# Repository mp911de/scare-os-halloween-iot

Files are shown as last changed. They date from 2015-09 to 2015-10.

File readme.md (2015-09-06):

ScareOS Halloween Pumpkin thingy
================================

Muhahahaha! Aaaaargh! Trick or Treat. Be so sweet. Give me something good to eat.

I wanted to build something cool and scary for Halloween. Here in Germany Helloween is just about to become a trend. Meet the ScareOS, a thingy to spice up Halloween.

**Features**

* Moving eyes (object tracking perhaps in version 2 - have to figure out how to integrate motion tracking)
* Discovers if someone is around by using a ranging sensor
* Plays Halloween sounds when it's awake
* Sleep state if no one is around for a while
* Whines when someone comes too close

ScareOS is an Arduino-based thingy with eyes, sound and a range sensor. ScareOS tends to be sleepy. It there's no one around, it sleeps and snores. As soon as someone comes into range, it awakens. Then the thingy looks at its visitor, triggers a series of Halloween sounds and, moves its eyes. But beware! It starts to cry like a baby when you approach too close.

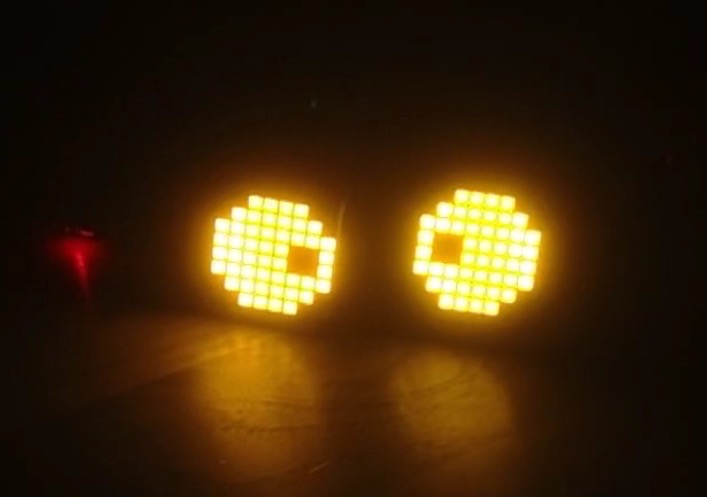
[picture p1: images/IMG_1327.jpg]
Glow in the dark


The components are not yet built into a Pumpkin, but they are ready to go. I'll provide pictures on Oct 31, once I got the pumpkin set up.

**Youtube Videos**

<a href="http://www.youtube.com/watch?feature=player_embedded&v=ZoHyhjCuUWQ
" target="_blank"></a>

<a href="http://www.youtube.com/watch?feature=player_embedded&v=dUIu-4qToRM
" target="_blank"></a>

*Hint: The video interferences are some recording issues.*

Ingredients
-----
You'll need:

* 1x Arduino (I used the [Ardunino Mini Pro](http://www.adafruit.com/products/2378) because of its form factor)
* 1x [Ultrasonic HC-SR04 Ranging Sensor](http://www.amazon.com/SainSmart-HC-SR04-Ranging-Detector-Distance/dp/B004U8TOE6)
* 2x [8X8 LED Matrix with I2C Backpack](http://www.adafruit.com/products/1050)
* 1x [Audio FX Sound Board - WAV/OGG Trigger with 2MB Flash](http://www.adafruit.com/products/2133)
* 1x 470µF Capacitor
* 1x 470Ω - 560Ω Resistor
* 1x 330Ω - 360Ω Resistor
* a [whole bunch](http://www.adafruit.com/products/826) of wire connectors
* 1x [Speaker](http://www.adafruit.com/products/1314)
* 1x [Breadboard](http://www.adafruit.com/products/64) (or a circuit board)

Once you have all parts together, you can start wiring them.

Wiring
------
The common ground and common `VCC` of the breadboard comes handy to provide current for the involved components. The diagram shows you how to connect the particular components.

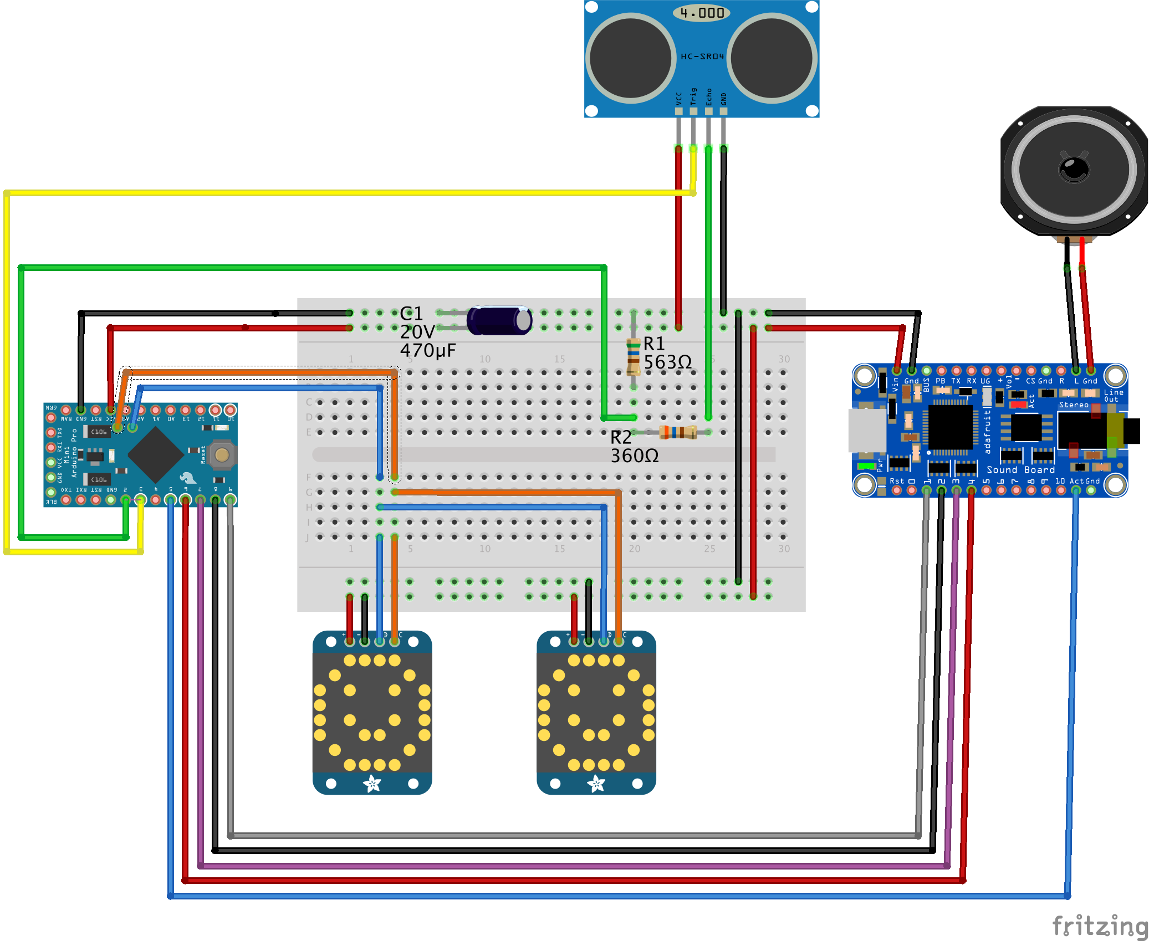
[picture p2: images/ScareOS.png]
Fritzing wiring diagram


The two resistors protect the circuit from a signal that won't come back. I originally built the ranging sensor circuit on RaspberryPi and took kept the design. The Arduino `pulseIn()` function also accepts a timeout so basically the circuit would work without the resistors.

The capacitor stabilizes the circuit. I discovered that the LED matrices cause some interference and instabilities within the `VCC`. The effect: The ranging sensor works only until some 80cm once both LED matrices are turned on. If the matrices are switched off or do not display anything, the ranging sensor works fine. My solution: Connect a capacitor to `GND` and `VCC`.

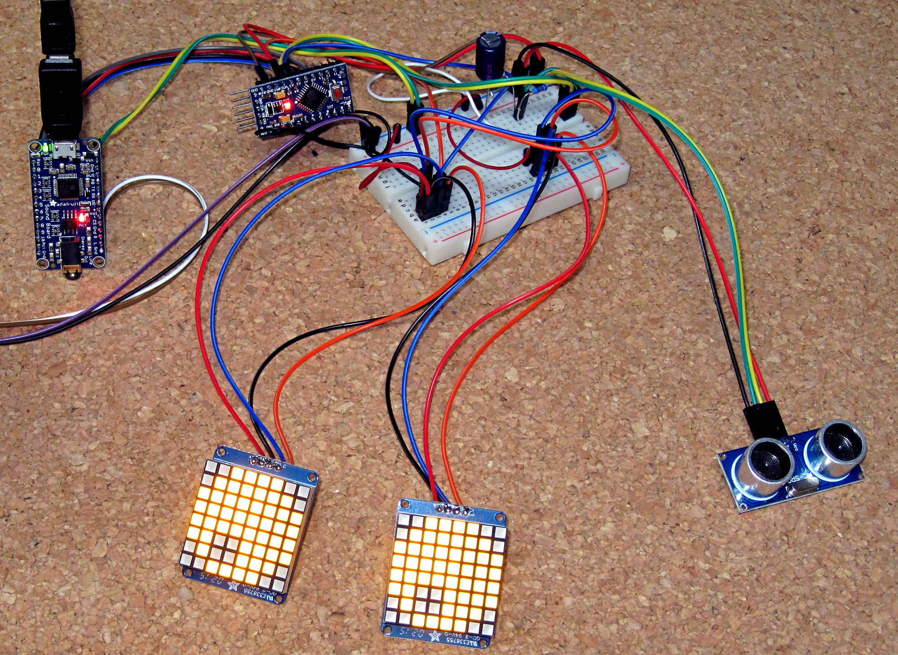
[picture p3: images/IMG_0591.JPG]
Connected components


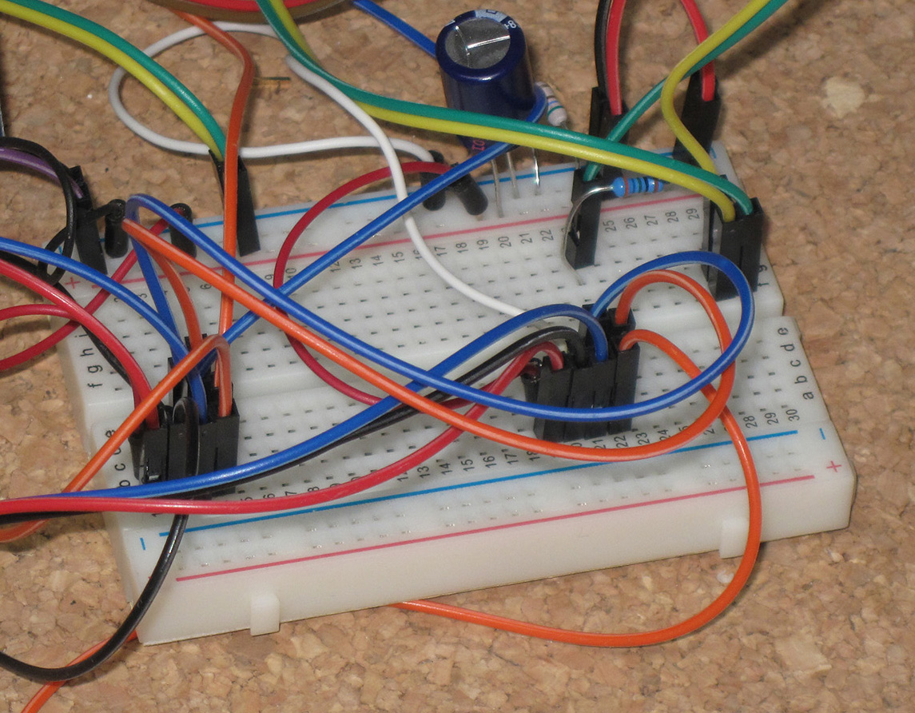
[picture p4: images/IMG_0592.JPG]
Closeup of the breadboard


Sounds
------
Once all parts are connected, upload the sounds from the `sounds` folder to the soundboard. Connect the soundboard to a USB port and copy all files to the flash disk using your favorite file copy tool.

There are four sounds/categories of sounds:

1. T01 Wake-up sound: Played once the ScareOS awakes from the sleep state
2. T02RANDnn sounds: Collection of sounds that are played randomly in the awake state. Therefore, the special suffix `RAND00` to `RAND99`
3. T03 sound: Whining/crying if someone approaches in the near zone of the device
4. T04HOLDL: Snoring sound, plays as long as the trigger is held, therefore, the special suffix `HOLDL`

Arduino Sketch
--------------

You need some code to run ScareOS. The code controls the components and handles wake/sleep, triggering sounds and displaying the eyes on the LED matrix.

The code is located in `scare-os/scare-os.ino`. You need two additional libraries:

* [Adafruit-LED-Backpack-Library](https://github.com/adafruit/Adafruit-LED-Backpack-Library)
* [Adafruit-GFX-Library](https://github.com/adafruit/Adafruit-GFX-Library)

The Adafruit site has a nice tutorial how to [install Arduino libraries](https://learn.adafruit.com/adafruit-all-about-arduino-libraries-install-use/arduino-libraries).

So open the Sketch, compile it and upload it to your Arduino.

You can adopt the code to use different pins or adjust the distance/timing:

```arduino
#define PIN_SONIC_TRIGGER 3
#define PIN_SONIC_ECHO 2

#define PIN_SND_TRIGGER_WAKE 9
#define PIN_SND_TRIGGER_REGULAR 8
#define PIN_SND_TRIGGER_NEAR 7
#define PIN_SND_TRIGGER_SLEEPING 6
#define PIN_SND_ACTIVE  5

// ms
#define SOUND_INTERVAL_MS 20000
#define WAKE_DURATION_MS 180000

#define ACTIVATION_DISTANCE_CM 280
#define NEAR_DISTANCE_CM 100
```

### Threading with Arduino

Arduino code runs only single-threaded, meaning your Arduino can do only one thing at a time. The sound trigger module, for instance, does not occupy the Arduino once a sound plays. So sounds play in the background within this terminology. Why am I telling you that? 

Displaying and animating graphics, like it is done with the matrix eyes, requires the Arduino to execute code, sleep a while, then execute code again and so on. One animation cycle lasts between 0.5sec and 10sec. In this time, the Arduino is occupied with the animation. If someone walks by the range sensor really fast, we would not notice it, because we're occupied with animating and not with measuring distance. 

But that's not fully true. Most of the time, the Arduino "sleeps" which means we could use that time to do different things - things like triggering a sound or measuring distance. The code is written to utilize these delays. You'll find lots of calls to a `bgProcessing()` method. This method is called with a delay parameter. If the delay is long enough to measure the distance (measuring the distance needs time and triggering sound, too), the distance is measured and the sound processing is invoked there. It's not exactly a task scheduler like a Windows or MacOS use to emulate multi-threading on one CPU (core), but it interleaves tasks in a similar way.

### Some words about measuring distance

The ranging sensor uses the physics of [speed of sound](https://en.wikipedia.org/wiki/Speed_of_sound) to determine the distance. An ultrasonic sound is triggered and the microphone records the echo. The speed of sound in dry air is about one kilometer in 2.914 sec. Since the sound needs to hit an object that bounces it back, the way is crossed twice. This means, that the duration to measure the distance is `DISTANCE * Speed of Sound * 2`.

Sometimes, the ranging sensor reports an echo after a shorer or longer time. The result of that are flickering distances of up to 100cm. These are outliers and falsify the result (the assumption of distance). The code, therefore, performs a series of measures, sorts the results and takes some middle result. It works pretty good and the implementation is quite simple (easier than calculating a quantile).

And now, it's time to scare:

<a href="http://www.youtube.com/watch?feature=player_embedded&v=ZoHyhjCuUWQ
" target="_blank"></a>

Attribution
-----------
I used following sound effects that require attribution:

* http://soundbible.com/1363-Angry-Cat.html
* http://soundbible.com/1939-Bats-In-Cave.html
* http://soundbible.com/2038-Demon-Girls-Mockingbird.html
* http://soundbible.com/1627-Female-Scream-Horror.html
* http://soundbible.com/1738-Little-Demon-Girl-Song.html
* http://soundbible.com/1828-Poltergeist.html
* http://soundbible.com/1918-Sick-Villain.html
* http://soundbible.com/766-Slow-Breathing.html
* http://soundbible.com/2016-Thunder-Strike-2.html

License
-----------
<br /><span xmlns:dct="http://purl.org/dc/terms/" property="dct:title">ScareOS</span> by <a xmlns:cc="http://creativecommons.org/ns#" href="https://github.com/mp911de/scare-os-halloween-iot" property="cc:attributionName" rel="cc:attributionURL">https://github.com/mp911de/scare-os-halloween-iot</a> is licensed under a <a rel="license" href="http://creativecommons.org/licenses/by/4.0/">Creative Commons Attribution 4.0 International License</a>.<br />Based on a work at <a xmlns:dct="http://purl.org/dc/terms/" href="https://github.com/mp911de/scare-os-halloween-iot" rel="dct:source">https://github.com/mp911de/scare-os-halloween-iot</a>.

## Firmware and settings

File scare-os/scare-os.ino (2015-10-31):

#include <Wire.h>
#include "Adafruit_LEDBackpack.h"
#include "Adafruit_GFX.h"

#define PIN_SONIC_TRIGGER 3
#define PIN_SONIC_ECHO 2

#define PIN_SND_TRIGGER_WAKE 9
#define PIN_SND_TRIGGER_REGULAR 8
#define PIN_SND_TRIGGER_NEAR 7
#define PIN_SND_TRIGGER_SLEEPING 6
#define PIN_SND_ACTIVE  5

Adafruit_8x8matrix matrix1 = Adafruit_8x8matrix();
Adafruit_8x8matrix matrix2 = Adafruit_8x8matrix();

// define eye ball without pupil
byte eyeBall[8] = {
  B00111100,
  B01111110,
  B11111111,
  B11111111,
  B11111111,
  B11111111,
  B01111110,
  B00111100
};

byte eyePupil = B11100111;

// stores current state of LEDs
byte eyeCurrent[8];
int currentX;
int currentY;


// min and max positions
#define MIN -2
#define MAX  2

// delays
#define DELAY_BLINK 40

// perform an effect every # of loop iterations, 0 to disable
#define EFFECT_ITERATION 4

// ms
#define SOUND_INTERVAL_MS 20000
#define WAKE_DURATION_MS 180000

#define ACTIVATION_DISTANCE_CM 280
#define NEAR_DISTANCE_CM 100

boolean awake = true;
long activatedMillis = 0;
long lastSound = 0;
boolean soundStarted = false;
long currentDistance = 0;

void setup() {
  Serial.begin(9600);
  Serial.println("Time to power up");
  
  
  Serial.println("       __J\"L__");
  Serial.println("   ,-\"`--...--'\"-.");
  Serial.println("  /  /\\       /\\  \\");
  Serial.println(" J  /__\\  _  /__\\  L");
  Serial.println(" |       / \\       |");
  Serial.println(" J    _  \"\"\"  _    F");
  Serial.println("  \\   \\|/\\_/\\|/   /");
  Serial.println("   \"-._\\/\\_/\\/_,-\"happy halloween!");
  

  pinMode(PIN_SONIC_TRIGGER, OUTPUT);
  pinMode(PIN_SONIC_ECHO, INPUT);

  pinMode(PIN_SND_TRIGGER_REGULAR, OUTPUT);
  pinMode(PIN_SND_TRIGGER_WAKE, OUTPUT);
  pinMode(PIN_SND_TRIGGER_NEAR, OUTPUT);
  pinMode(PIN_SND_TRIGGER_SLEEPING, OUTPUT);
  pinMode(PIN_SND_ACTIVE, INPUT);

  digitalWrite(PIN_SND_TRIGGER_REGULAR, HIGH);
  digitalWrite(PIN_SND_TRIGGER_WAKE, HIGH);
  digitalWrite(PIN_SND_TRIGGER_NEAR, HIGH);
  digitalWrite(PIN_SND_TRIGGER_SLEEPING, HIGH);

  matrix1.begin(0x70);  // pass in the address
  matrix2.begin(0x71);  // pass in the address

  // LED test
  // vertical line
  byte b = B10000000;
  for (int c = 0; c <= 7; c++)
  {
    for (int r = 0; r <= 7; r++)
    {
      setRow(0, r, b);
      setRow(1, r, b);
    }
    b = b >> 1;
    writeMatrix();
    delay(20);
  }
  // full module
  b = B11111111;
  for (int r = 0; r <= 7; r++)
  {
    setRow(0, r, b);
    setRow(1, r, b);
  }

  writeMatrix();

  // clear both modules
  matrix1.setBrightness(16);
  matrix1.clear();
  matrix2.setBrightness(16);
  matrix2.clear();
  delay(500);

  // random seed
  randomSeed(analogRead(0));

  // center eyes
  displayEyes(0, 0);
  activatedMillis = 0;
  Serial.println("ScareOS ready.");
}

/*
  Arduino loop
*/
void loop()
{

  long awakeDurationMs = getAwakeDurationMs();

  if (awakeDurationMs > WAKE_DURATION_MS) {
    if (awake) {
      awake = false;
      Serial.println("Going to sleep");
      moveEyes(0, -4, 10);
      reduceBrightness();
    }
  }

  if (!awake) {
    slightGlow();
    bgProcessing(random(5, 7) * 500);
    return;
  }

  matrix1.setBrightness(16);
  matrix2.setBrightness(16);

  // move to random position, wait random time
  moveEyes(random(MIN, MAX + 1), random(MIN, MAX + 1), 50);
  bgProcessing(random(5, 7) * 500);

  // blink time?
  if (random(0, 5) == 0) {
    bgProcessing(500);
    blinkEyes();
    bgProcessing(500);
  }

  int effect = random(0, 10);
  switch (effect) {
    case 0: // cross eyes
      crossEyes();
      break;

    case 1: // round spin
      roundSpin(2);
      break;

    case 2: // crazy spin
      crazySpin(2);
      break;

    case 3: // meth eyes
      methEyes();
      break;

    case 4: // lazy eye
      lazyEye();
      break;

    case 5: // crazy blink
      blinkEyes(true, false);
      blinkEyes(false, true);
      break;

    case 6: // glow
      glowEyes(3);
      break;

    default:
      break;
  }

  bgProcessing(1000);
}

long getAwakeDurationMs() {
  return millis() - activatedMillis;
}

/*
Background-processing:
1. get distance if allowed timeToComeBack is greater the duration needed to measure distance
2. Trigger awake sound
3. Trigger sounds if necessary
4. Delay until timeToComeBack is passed by

*/
void bgProcessing(long timeToComeBack) {

  long start = millis();

  if (timeToComeBack > 100) {
    currentDistance = getFilteredDistance();
    long duration = millis() - start;
    Serial.print("Duration: ");
    Serial.print(duration);
    Serial.print("ms/");

    Serial.print("Distance: ");
    Serial.print(currentDistance);
    Serial.println("cm");
  }

  // activate either by distance or randomly
  if (currentDistance < ACTIVATION_DISTANCE_CM) {
    activatedMillis = millis();

    if (!awake) {
      Serial.println("Wakeup now");
      disableSleepSound();
      delay(20);
      triggerSound(PIN_SND_TRIGGER_WAKE);
      awake = true;
    }
  }

  Serial.print("Awake: ");
  Serial.print(awake);
  Serial.print("/Currently awake since ");
  Serial.print(getAwakeDurationMs());
  Serial.println("ms");

  soundProcessing();

  long duration = millis() - start;
  long sleepTimeLeft = timeToComeBack - duration;
  if (sleepTimeLeft > 100) {
    delay(20);
    bgProcessing(sleepTimeLeft - 20);
    return;
  }
  if (sleepTimeLeft > 0) {
    delay(sleepTimeLeft);
  }
}


// Performs a multi-measure of the distance and returns the 3rd highest value.
long getFilteredDistance() {
  int rangevalue[] = { 0, 0, 0, 0, 0};
  int arraysize = 5;

  for (int i = 0; i < arraysize; i++) {
    rangevalue[i] = distance();
    delay(10);
  }

  isort(rangevalue, arraysize);
  int distance = ifilter(rangevalue, arraysize);

  return distance;
}

long distance() {
  long duration, distance;
  digitalWrite(PIN_SONIC_TRIGGER, LOW);
  delayMicroseconds(2);
  digitalWrite(PIN_SONIC_TRIGGER, HIGH);
  delayMicroseconds(10);
  digitalWrite(PIN_SONIC_TRIGGER, LOW);

  duration = pulseIn(PIN_SONIC_ECHO, HIGH);
  distance = (duration / 2) / 29.1;
  return distance;
}

//Sorting function
// sort function (Author: Bill Gentles, Nov. 12, 2010)
void isort(int *a, int n) {
  // *a is an array pointer function
  for (int i = 1; i < n; ++i)
  {
    int j = a[i];
    int k;
    for (k = i - 1; (k >= 0) && (j < a[k]); k--)
    {
      a[k + 1] = a[k];
    }
    a[k + 1] = j;
  }
}

// return the 2nd highest distance
int ifilter(int *x, int n) {
  return x[n - 2];
}


/*
Sound handling
1. Check if sound is playing. If so, return
2. trace timestamp of last sound playing
3. Play sleep sound if system is not "awake"
4. Play whining sound if someone comes to near
5. Play random sounds if system is "awake"
*/
void soundProcessing() {
  
  if (!awake) {
    enableSleepSound();
    return;
  }

  disableSleepSound();
  
  if (isSoundPlaying()) {
    return;
  }

  if (soundStarted) {
    soundStarted = false;
    lastSound = millis();
    return;
  }

  if (currentDistance > 0 && currentDistance < NEAR_DISTANCE_CM) {
    triggerSound(PIN_SND_TRIGGER_NEAR);
    return;
  }

  long soundInterval = millis() - lastSound;
  if (lastSound == 0 || soundInterval > SOUND_INTERVAL_MS) {
    triggerSound(PIN_SND_TRIGGER_REGULAR);
  }
}

void enableSleepSound(){
  digitalWrite(PIN_SND_TRIGGER_SLEEPING, LOW);
}

void disableSleepSound(){
  digitalWrite(PIN_SND_TRIGGER_SLEEPING, HIGH);
  delay(10);
}

void triggerSound(int pin) {
  Serial.print("triggerSound(");
  Serial.print(pin);
  Serial.println(")");

  digitalWrite(pin, LOW);
  delay(200);
  digitalWrite(pin, HIGH);
  delay(100);
  soundStarted = true;
}

/*
 True if the sound is playing.
 */
boolean isSoundPlaying() {
  if (digitalRead(PIN_SND_ACTIVE) == 0) {
    return true;
  }
  return false;
}


/*
  This method blinks both eyes
*/
void blinkEyes()
{
  blinkEyes(true, true);
}

/*
  This method blinks eyes as per provided params
*/
void blinkEyes(boolean blinkLeft, boolean blinkRight)
{
  // blink?
  if (!blinkLeft && !blinkRight)
    return;

  // close eyelids
  for (int i = 0; i <= 3; i++)
  {
    if (blinkLeft)
    {
      setRow(0, i, 0);
      setRow(0, 7 - i, 0);
    }
    if (blinkRight)
    {
      setRow(1, i, 0);
      setRow(1, 7 - i, 0);
    }
    writeMatrix();
    delay(DELAY_BLINK);
  }

  // open eyelids
  for (int i = 3; i >= 0; i--)
  {
    if (blinkLeft)
    {
      setRow(0, i, eyeCurrent[i]);
      setRow(0, 7 - i, eyeCurrent[7 - i]);
    }
    if (blinkRight)
    {
      setRow(1, i, eyeCurrent[i]);
      setRow(1, 7 - i, eyeCurrent[7 - i]);
    }
    writeMatrix();
    delay(DELAY_BLINK);
  }
}

/*
  This methods moves eyes to center position,
  then moves horizontally with wrapping around edges.
*/
void crazySpin(int times)
{
  if (times == 0)
    return;

  moveEyes(0, 0, 50);
  bgProcessing(500);

  byte row = eyePupil;
  for (int t = 0; t < times; t++)
  {
    // spin from center to L
    for (int i = 0; i < 5; i++)
    {
      row = row >> 1;
      row = row | B10000000;
      setRow(0, 3, row);  setRow(1, 3, row);
      setRow(0, 4, row);  setRow(1, 4, row);
      writeMatrix();
      bgProcessing(50);
      if (t == 0)
        bgProcessing((5 - i) * 10); // increase delay on 1st scroll (speed up effect)
    }
    // spin from R to center
    for (int i = 0; i < 5; i++)
    {
      row = row >> 1;
      if (i >= 2)
        row = row | B10000000;
      setRow(0, 3, row);  setRow(1, 3, row);
      setRow(0, 4, row);  setRow(1, 4, row);
      writeMatrix();
      bgProcessing(50);
      if (t == (times - 1))
        bgProcessing((i + 1) * 10); // increase delay on last scroll (slow down effect)
    }
  }
}

/*
  This method crosses eyes
*/
void crossEyes()
{
  moveEyes(0, 0, 50);
  bgProcessing(500);

  byte pupilR = eyePupil;
  byte pupilL = eyePupil;

  // move pupils together
  for (int i = 0; i < 2; i++)
  {
    pupilR = pupilR >> 1;
    pupilR = pupilR | B10000000;
    pupilL = pupilL << 1;
    pupilL = pupilL | B1;

    setRow(0, 3, pupilR); setRow(1, 3, pupilL);
    setRow(0, 4, pupilR); setRow(1, 4, pupilL);

    writeMatrix();
    bgProcessing(100);
  }

  bgProcessing(2000);

  // move pupils back to center
  for (int i = 0; i < 2; i++)
  {
    pupilR = pupilR << 1;
    pupilR = pupilR | B1;
    pupilL = pupilL >> 1;
    pupilL = pupilL | B10000000;

    setRow(0, 3, pupilR); setRow(1, 3, pupilL);
    setRow(0, 4, pupilR); setRow(1, 4, pupilL);
    
    writeMatrix();
    bgProcessing(100);
  }
}

/*
  This method displays eyeball with pupil offset by X, Y values from center position.
  Valid X and Y range is [MIN,MAX]
  Both LED modules will show identical eyes
*/
void displayEyes(int offsetX, int offsetY)
{
  // ensure offsets are  in valid ranges
  offsetX = getValidValue(offsetX);
  offsetY = getValidValue(offsetY);

  // calculate indexes for pupil rows (perform offset Y)
  int row1 = 3 - offsetY;
  int row2 = 4 - offsetY;

  // define pupil row
  byte pupilRow = eyePupil;

  // perform offset X
  // bit shift and fill in new bit with 1
  if (offsetX > 0) {
    for (int i = 1; i <= offsetX; i++)
    {
      pupilRow = pupilRow >> 1;
      pupilRow = pupilRow | B10000000;
    }
  }
  else if (offsetX < 0) {
    for (int i = -1; i >= offsetX; i--)
    {
      pupilRow = pupilRow << 1;
      pupilRow = pupilRow | B1;
    }
  }

  // pupil row cannot have 1s where eyeBall has 0s
  byte pupilRow1 = pupilRow & eyeBall[row1];
  byte pupilRow2 = pupilRow & eyeBall[row2];

  // display on LCD matrix, update to eyeCurrent
  for (int r = 0; r < 8; r++)
  {
    if (r == row1)
    {
      setRow(0, r, pupilRow1);
      setRow(1, r, pupilRow1);
      eyeCurrent[r] = pupilRow1;
    }
    else if (r == row2)
    {
      setRow(0, r, pupilRow2);
      setRow(1, r, pupilRow2);
      eyeCurrent[r] = pupilRow2;
    }
    else
    {
      setRow(0, r, eyeBall[r]);
      setRow(1, r, eyeBall[r]);
      eyeCurrent[r] = eyeBall[r];
    }
  }
  
  writeMatrix();
  // update current X and Y
  currentX = offsetX;
  currentY = offsetY;
}

/*
  This method corrects provided coordinate value
*/
int getValidValue(int value)
{
  if (value > MAX)
    return MAX;
  else if (value < MIN)
    return MIN;
  else
    return value;
}

/*
  This method pulsates eye (changes LED brightness)
*/
void glowEyes(int times)
{
  for (int t = 0; t < times; t++)
  {
    for (int i = 2; i <= 16; i++)
    {
      matrix1.setBrightness(i);
      matrix2.setBrightness(i);
      delay(50);
    }

    bgProcessing(250);

    reduceBrightness();

    bgProcessing(150);
  }

  for (int i = 2; i <= 16; i++)
  {
    matrix1.setBrightness(i);
    matrix2.setBrightness(i);
    delay(50);
  }

  matrix1.setBrightness(16);
  matrix2.setBrightness(16);
}

void reduceBrightness() {
  for (int i = 16; i >= 1; i--) {
    matrix1.setBrightness(i);
    matrix2.setBrightness(i);
    delay(25);
  }
}

/*
  This method pulsates eye  (changes LED brightness)
*/
void slightGlow()
{
  for (int i = 1; i <= 5; i++)
  {
    matrix1.setBrightness(i);
    matrix2.setBrightness(i);
    delay(150);
  }

  bgProcessing(250);

  for (int i = 5; i >= 1; i--) {
    matrix1.setBrightness(i);
    matrix2.setBrightness(i);
    delay(150);
  }
}

/*
  This method moves eyes to center, out and then back to center
*/
void methEyes()
{
  moveEyes(0, 0, 50);
  bgProcessing(500);

  byte pupilR = eyePupil;
  byte pupilL = eyePupil;

  // move pupils out
  for (int i = 0; i < 2; i++)
  {
    pupilR = pupilR << 1;
    pupilR = pupilR | B1;
    pupilL = pupilL >> 1;
    pupilL = pupilL | B10000000;

    setRow(0, 3, pupilR); setRow(1, 3, pupilL);
    setRow(0, 4, pupilR); setRow(1, 4, pupilL);
    writeMatrix();
    bgProcessing(100);
  }

  bgProcessing(2000);

  // move pupils back to center
  for (int i = 0; i < 2; i++)
  {
    pupilR = pupilR >> 1;
    pupilR = pupilR | B10000000;
    pupilL = pupilL << 1;
    pupilL = pupilL | B1;

    setRow(0, 3, pupilR); setRow(1, 3, pupilL);
    setRow(0, 4, pupilR); setRow(1, 4, pupilL);
    writeMatrix();
    bgProcessing(100);
  }
}

/*
  This method moves both eyes from current position to new position
*/
void moveEyes(int newX, int newY, int stepDelay)
{
  // set current position as start position
  int startX = currentX;
  int startY = currentY;

  // fix invalid new X Y values
  newX = getValidValue(newX);
  newY = getValidValue(newY);

  // eval steps
  int stepsX = abs(currentX - newX);
  int stepsY = abs(currentY - newY);

  // need to change at least one position
  if ((stepsX == 0) && (stepsY == 0))
    return;

  // eval direction of movement, # of steps, change per X Y step, perform move
  int dirX = (newX >= currentX) ? 1 : -1;
  int dirY = (newY >= currentY) ? 1 : -1;
  int steps = (stepsX > stepsY) ? stepsX : stepsY;
  int intX, intY;
  float changeX = (float)stepsX / (float)steps;
  float changeY = (float)stepsY / (float)steps;
  for (int i = 1; i <= steps; i++)
  {
    intX = startX + round(changeX * i * dirX);
    intY = startY + round(changeY * i * dirY);
    displayEyes(intX, intY);
    bgProcessing(stepDelay);
  }
}

/*
  This method lowers and raises right pupil only
*/
void lazyEye()
{
  moveEyes(0, 1, 50);
  bgProcessing(500);

  // lower left pupil slowly
  for (int i = 0; i < 3; i++)
  {
    setRow(1, i + 2, eyeBall[i + 2]);
    setRow(1, i + 3, eyeBall[i + 3] & eyePupil);
    setRow(1, i + 4, eyeBall[i + 4] & eyePupil);
    writeMatrix();
    bgProcessing(150);
  }

  bgProcessing(1000);

  // raise left pupil quickly
  for (int i = 0; i < 3; i++)
  {
    setRow(1, 4 - i, eyeBall[4 - i] & eyePupil);
    setRow(1, 5 - i, eyeBall[5 - i] & eyePupil);
    setRow(1, 6 - i, eyeBall[6 - i]);
    writeMatrix();
    bgProcessing(25);
  }
}

/*
  This method spins pupils clockwise
*/
void roundSpin(int times)
{
  if (times == 0)
    return;

  moveEyes(2, 0, 50);
  bgProcessing(500);

  for (int i = 0; i < times; i++)
  {
    displayEyes(2, -1); delay(40); if (i == 0) delay(40);
    displayEyes(1, -2); delay(40); if (i == 0) delay(30);
    displayEyes(0, -2); delay(40); if (i == 0) delay(20);
    displayEyes(-1, -2); delay(40); if (i == 0) delay(10);
    displayEyes(-2, -1); delay(40);
    displayEyes(-2, 0); delay(40);
    displayEyes(-2, 1); delay(40); if (i == (times - 1)) delay(10);
    displayEyes(-1, 2); delay(40); if (i == (times - 1)) delay(20);
    displayEyes(0, 2); delay(40); if (i == (times - 1)) delay(30);
    displayEyes(1, 2); delay(40); if (i == (times - 1)) delay(40);
    displayEyes(2, 1); delay(40); if (i == (times - 1)) bgProcessing(50);
    displayEyes(2, 0); delay(40);
  }
}


void writeMatrix(){
    matrix1.writeDisplay();
    matrix2.writeDisplay();
}

/*
  This method sets values to matrix row
  Performs 180 rotation if needed
*/
void setRow(int addr, int row, byte rowValue)
{

  for (int i = 0; i < 8; i++)
  {
    int val = rowValue & 1 << i;
    if (addr == 0)
      matrix1.drawPixel(row, i, val);
    if (addr == 1)
      matrix2.drawPixel(row, i, val);

  }


  //lc.setRow(addr, row, rowValue);
}


/*
  Reverse bits in byte
  http://www.nrtm.org/index.php/2013/07/25/reverse-bits-in-a-byte/
*/
byte bitswap (byte x)
{
  byte result;

  asm("mov __tmp_reg__, %[in] \n\t"
      "lsl __tmp_reg__  \n\t"   /* shift out high bit to carry */
      "ror %[out] \n\t"  /* rotate carry __tmp_reg__to low bit (eventually) */
      "lsl __tmp_reg__  \n\t"   /* 2 */
      "ror %[out] \n\t"
      "lsl __tmp_reg__  \n\t"   /* 3 */
      "ror %[out] \n\t"
      "lsl __tmp_reg__  \n\t"   /* 4 */
      "ror %[out] \n\t"

      "lsl __tmp_reg__  \n\t"   /* 5 */
      "ror %[out] \n\t"
      "lsl __tmp_reg__  \n\t"   /* 6 */
      "ror %[out] \n\t"
      "lsl __tmp_reg__  \n\t"   /* 7 */
      "ror %[out] \n\t"
      "lsl __tmp_reg__  \n\t"   /* 8 */
      "ror %[out] \n\t"
      : [out] "=r" (result) : [in] "r" (x));
  return (result);
}
